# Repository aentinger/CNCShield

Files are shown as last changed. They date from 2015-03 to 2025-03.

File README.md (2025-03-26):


💾 CNC Shield
=============



# 📸 Image

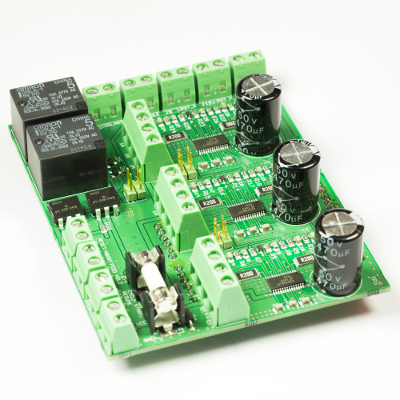
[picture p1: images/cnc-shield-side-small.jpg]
LXRobotics P11 CNC Shield


# 📂 Description

Until very recently the operation of CNC milling machines was reserved mainly for companies and individuals with large budget. However, in the last couple of years, an increasing trend towards self-made (DIY) CNC-milling machines could be observed. As a result from this observation LXRobotics developed the CNC Shield. The CNC-Shield is based on the grbl project, which allows the processing of gcode-control commands and generation of stepper motor control signals for a 3-axis CNC-milling machine with an Arduino Uno.

In order to demonstrate how easy a normal mill can be converted into a CNC mill we decided to convert the Proxxon MF70, a very popular milling machine amongst RC enthusiasts, into a full-fledged CNC-milling machine by using our CNC shield. The conversion with all necessary steps is well documented on our blog. Furthermore, extensive tutorials allow easy integration of our CNC  shields in any DIY-CNC project.

**Features**

* Control of 3 bipolar stepper motors with 2.5 A phase current at a maximum of 35 V (e.g.: NEMA17)
* Milling motor and coolant pump can be turned on/off via relays
* Limit switch for X, Y and Z-axis can be attached
* Cycle Start/Resume, Feed Hold and Reset/Abort switches can be attached
* grbl-compatible
* High qualits screw terminals for stable and durable connection of cables to the board
* 8A Fuse on board

Note
* Active cooling of the stepper motor driver is recommended.

# 🎥 [Video](images/cnc_shield_demo.mp4)

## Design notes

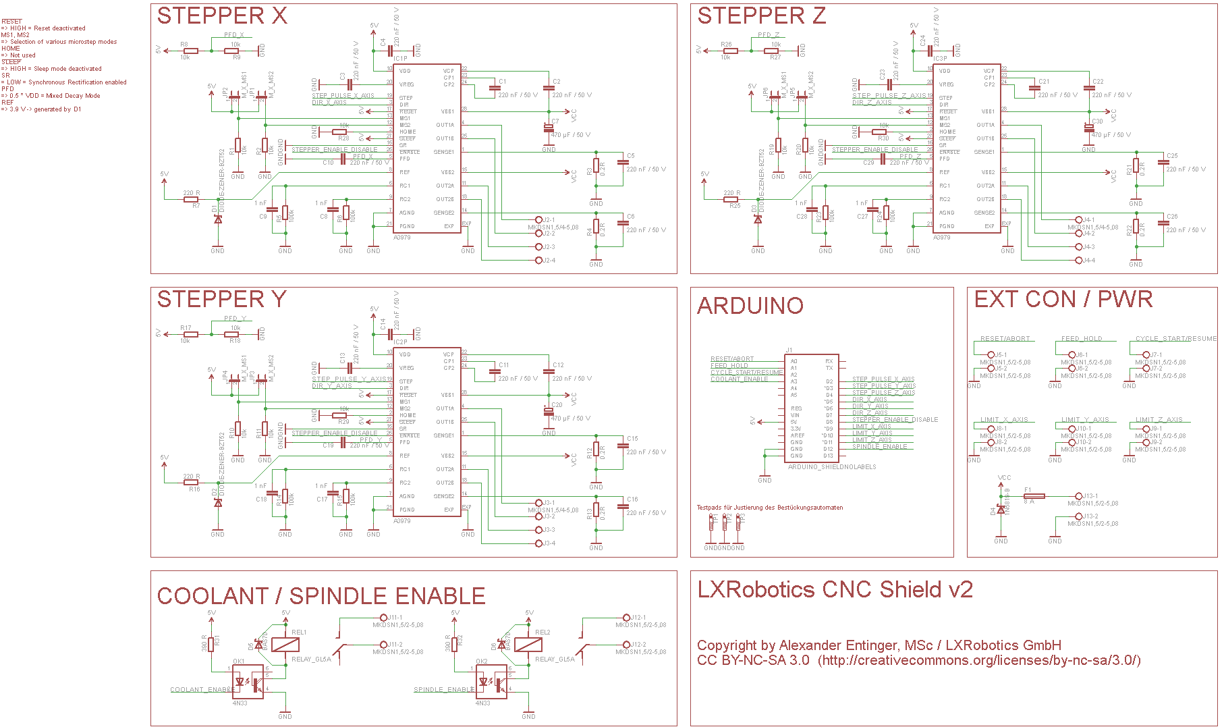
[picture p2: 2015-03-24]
hardware/lxrobotics_cnc_shield_v2.png

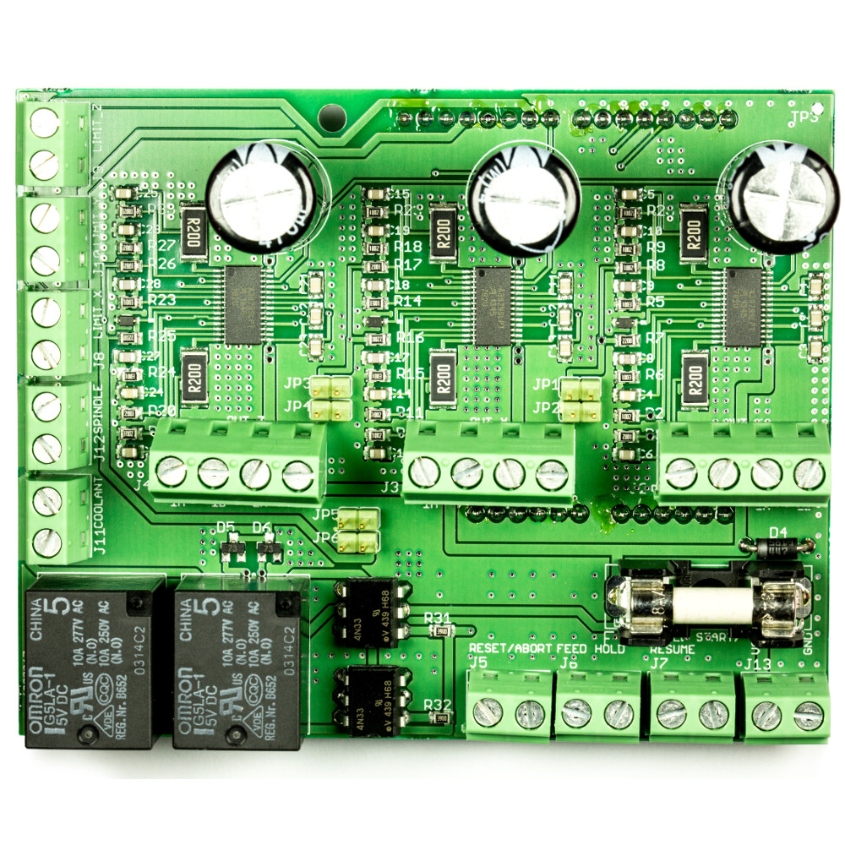
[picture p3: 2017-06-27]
images/cnc-shield-top-large.jpg

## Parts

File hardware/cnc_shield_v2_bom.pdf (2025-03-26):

Menge | Schaltplan | Bezeichnung | Farnell Bestell Nummer | Preis (1 Stück) | Gesamtpreis | Wird bestückt | Footprint | Säckchen
3 | IC1P,IC2P,IC3P | A3979, Stepper-Motortreiber, 2.5 A, 35 V, TSSOP28 | 1521716 | € 9,31 | € 27,93 | x
3 | | Kühlkörper für A3979 | 4302175 | € 0,81 | € 2,43 | | | S1
2 | J1 | Arduino Stiftleisten, 1x6, 2.54 mm | 1022255 | € 0,37 | € 0,74 | | | S2
2 | J1 | Arduino Stiftleisten, 1x8, 2.54 mm | 1022257 | € 0,19 | € 0,38 | | | S2
21 | C1,C2,C3,C4,C5,C6,C10,C11,C12,C13,C14,C15,C16,C19,C21,C22,C23,C24,C25,C26,C29 | Kondensator, 220 nF, 50V, 0805 | 2320842 | € 0,05 | € 0,97 | x
15 | R1,R2,R8,R9,R10,R11,R17,R18,R19,R20,R26,R27,R28,R29,R30 | Widerstand 10 k, 0805 | 1469856 | € 0,02 | € 0,33 | x
6 | JP1,JP2,JP3,JP4,JP5,JP6 | Stiftleiste, 2 Polig, 2.54 mm | 3418285 | € 0,24 | € 1,44 | | | S2
6 | | Jumper, 2 Polig, 2.54 mm | 4218176 | € 0,14 | € 0,84 | | | S2
6 | R3,R4,R12,R13,R21,R22 | Widerstand 0.2R, 2W, 2512 | 2328177 | € 0,26 | € 1,55 | x
3 | J2,J3,J4 | Schraubklemme, 4 Polig, MKDS 1,5/4-5,08 | 3041542 | € 1,94 | € 5,82 | | | S3
3 | C7,C20,C30 | Aluminium-Elko, 470 uF, 50 V | 1902936 | € 0,35 | € 1,06 | | | S4
6 | R5,R6,R14,R15,R23,R24 | Widerstand, 0805, 100 kOhm | 9332405 | € 0,01 | € 0,04 | x
6 | C8,C9,C17,C18,C27,C28 | Kondensator, 1 nF, 100 V, 0805 | 1759287 | € 0,02 | € 0,11 | x
3 | D1,D2,D3 | Z-Diode, BZT52, 3.9V, 5 mA | 2077925 | € 0,05 | € 0,15 | x
3 | R7,R16,R25 | Widerstand, 0805, 220 R | 9334130 | € 0,01 | € 0,02 | x
9 | J5,J6,J7,J8,J9,J10,J11,J12,J13 | Schraubklemme, 2 Polig, MKDS 1,5/2-5,08 | 3041440 | € 0,81 | € 7,31 | | | S3
1 | D4 | 1N5819, Vreverse = 40 V, If = 1 A | 9801219 | € 0,22 | € 0,22 | | | S5
2 | D5,D6 | BAS70, Diode Shottkey, Relais Freilaufdiode | 1797834 | € 0,09 | € 0,17 | x
2 | R31,R32 | Widerstand, 0805, 390 Ohm | 9334475 | € 0,01 | € 0,01 | x
2 | REL1,REL2 | GL5A Leistungsrelais, 5 VDC, 250 V AC, 10 A, RCOIL = 70 R | 1455502 | € 1,43 | € 2,86 | | | S6
2 | OK1,OK2 | 4N33, Optokoppler mit Photo-Darlington, DIL06 | 1469601 | € 0,45 | € 0,90 | | | S5
1 | F1 | Sicherungshalter 5 x 20 mm | 1162740 | € | 0,56 | € | 0,56 | S2
1 | F1 | Sicherung, 5x20, 8A, 250 V | 1354596 | € | 0,65 | € | 0,65
1 | Leitfähiger Schaumstoff | 1687855 | € | 2,40 | € | 2,40 | - | Bestellung von 1 Stück für 50 CNC Shields ausreichend
Summe | € | 58,90

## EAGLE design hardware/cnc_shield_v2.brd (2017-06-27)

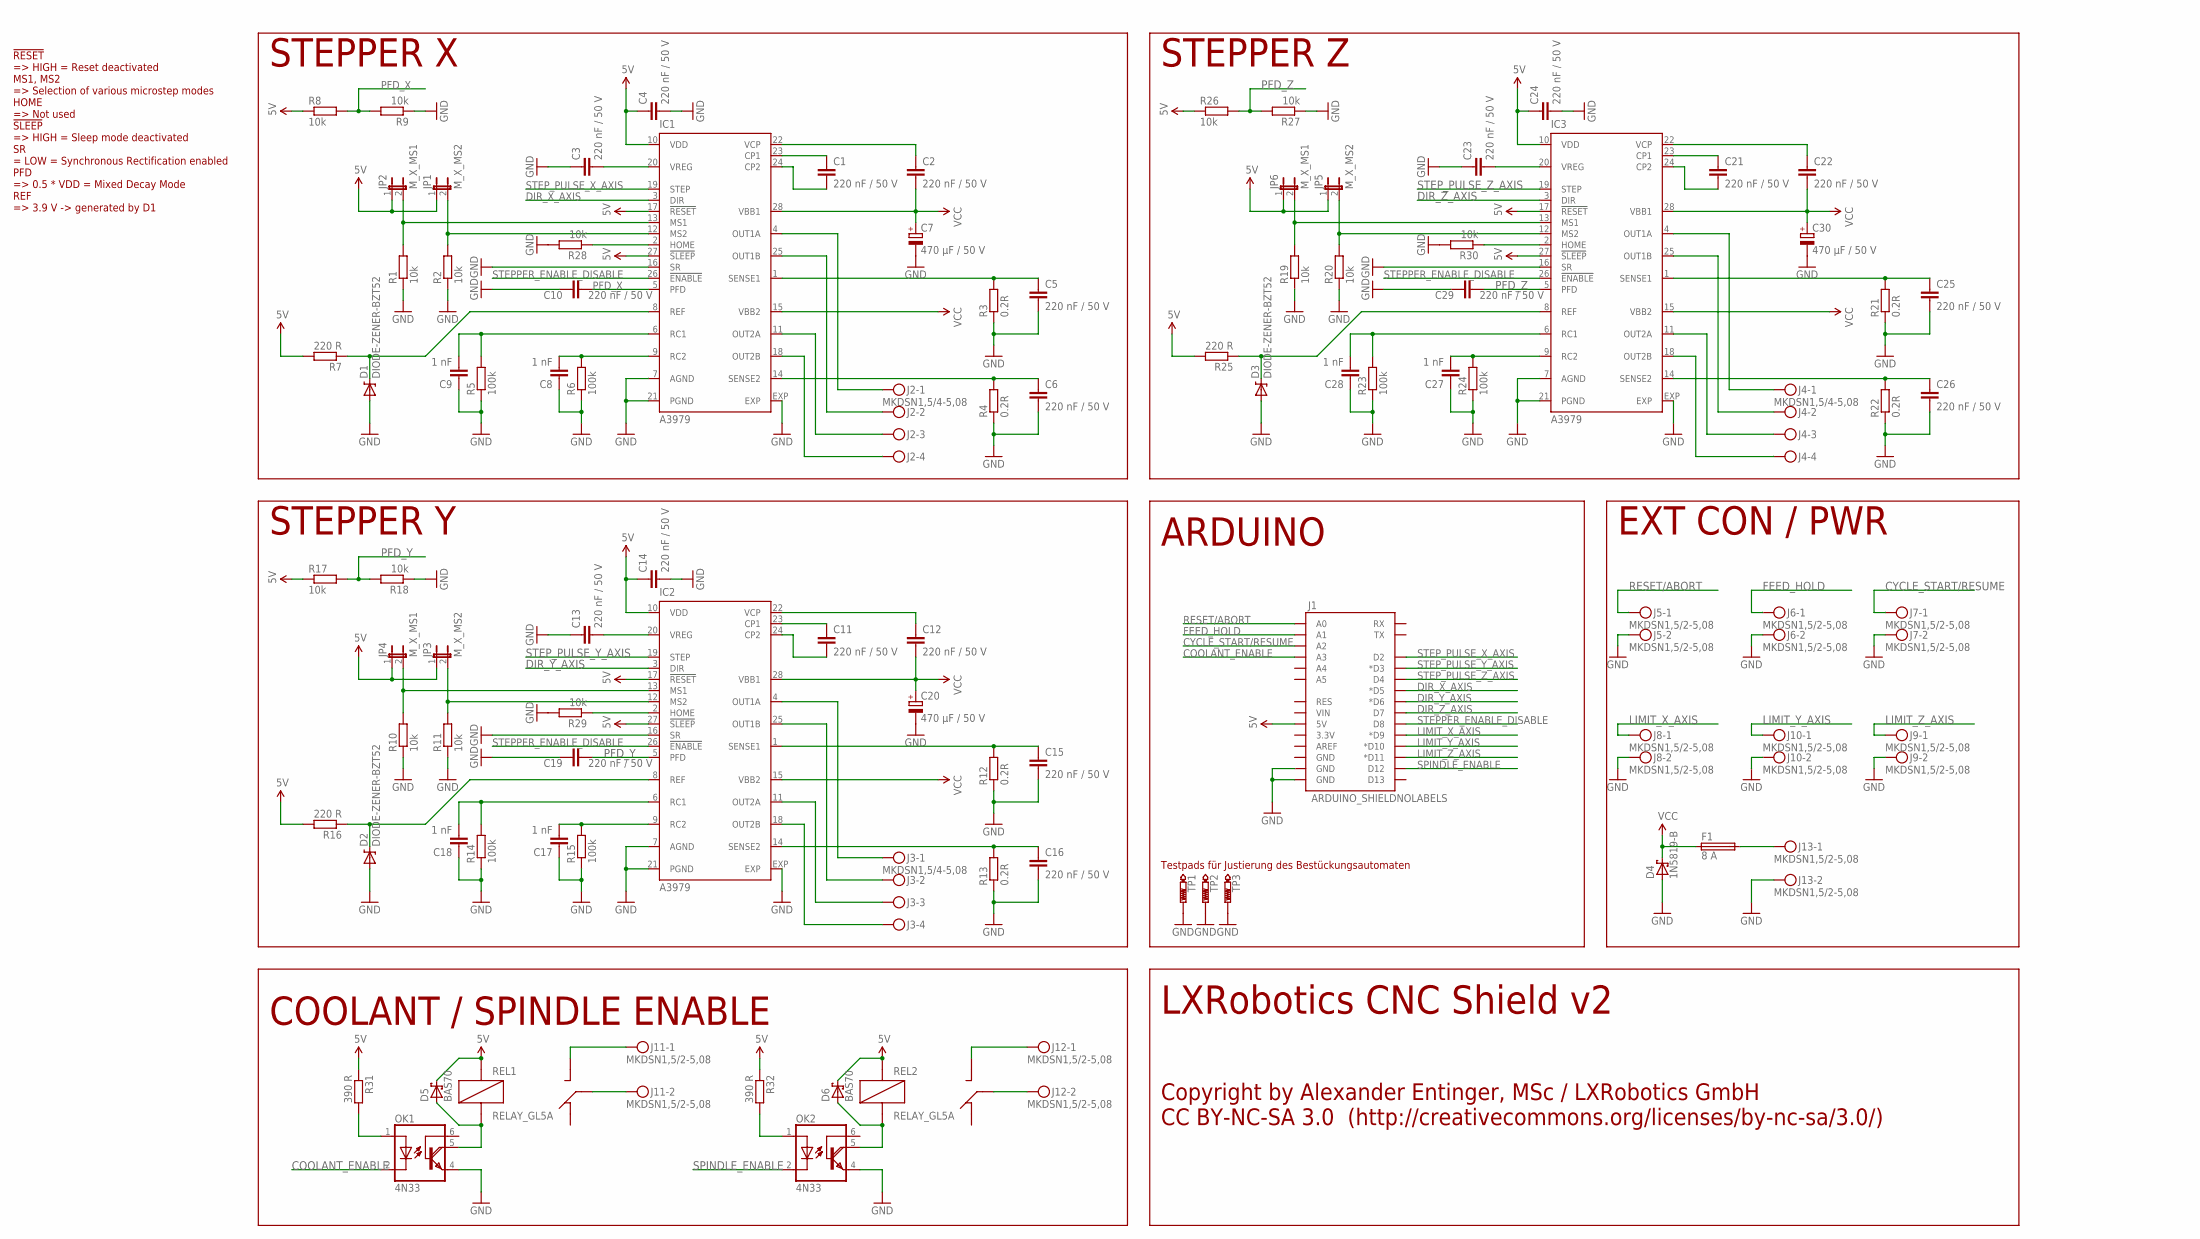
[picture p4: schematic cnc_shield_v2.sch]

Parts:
C1, C2, C3, C4, C5, C6, C10, C11, C12, C13, C14, C15, C16, C19, C21, C22, C23, C24, C25, C26, C29: 220 nF / 50 V; C0805K
C7, C20, C30: 470 µF / 50 V; E5-13
C8, C9, C17, C18, C27, C28: 1 nF; C0805K
D1, D2, D3: DIODE-ZENER-BZT52; SOD-323
D4: 1N5819-B; DO41-7.6
D5, D6: BAS70; SOT23
F1: 8 A; SH22,5
IC1, IC2, IC3: A3979; TSSOP28
J1: ARDUINO_SHIELDNOLABELS; DUEMILANOVE_SHIELD_NOLABELS
J2, J3, J4: MKDSN1,5/4-5,08
J5, J6, J7, J8, J9, J10, J11, J12, J13: MKDSN1,5/2-5,08
JP1, JP3, JP5: M_X_MS2; JP1
JP2, JP4, JP6: M_X_MS1; JP1
OK1, OK2: 4N33; DIL06
R1, R2, R8, R9, R10, R11, R17, R18, R19, R20, R26, R27, R28, R29, R30: 10k; R0805
R3, R4, R12, R13, R21, R22: 0.2R; R2512
R5, R6, R14, R15, R23, R24: 100k; R0805
R7, R16, R25: 220 R; R0805
R31, R32: 390 R; R0805
REL1, REL2: RELAY_GL5A
TP1, TP2, TP3: PTR1B1,27; B1,27

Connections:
5V: C4.1, C14.1, C24.1, D5.3 (C), D6.3 (C), IC1.10 (VDD), IC1.17 (!RESET), IC1.27 (!SLEEP), IC2.10 (VDD), IC2.17 (!RESET), IC2.27 (!SLEEP), IC3.10 (VDD), IC3.17 (!RESET), IC3.27 (!SLEEP), J1.5V, JP1.1, JP2.1, JP3.1, JP4.1, JP5.1, JP6.1, R7.2, R8.1, R16.2, R17.1, R25.2, R26.1, R31.1, R32.1, REL1.R2 (R2_COIL1), REL2.R2 (R2_COIL1)
COOLANT_ENABLE: J1.A3, OK1.2 (C)
CYCLE_START/RESUME: J1.A2, J7.1
DIR_X_AXIS: IC1.3 (DIR), J1.D5 (*D5)
DIR_Y_AXIS: IC2.3 (DIR), J1.D6 (*D6)
DIR_Z_AXIS: IC3.3 (DIR), J1.D7
FEED_HOLD: J1.A1, J6.1
GND: C3.1, C4.2, C5.2, C6.2, C7.-, C8.1, C9.1, C10.1, C13.1, C14.2, C15.2, C16.2, C17.1, C18.1, C19.1, C20.-, C23.1, C24.2, C25.2, C26.2, C27.1, C28.1, C29.1, C30.-, D1.2 (A), D2.2 (A), D3.2 (A), D4.A, IC1.7 (AGND), IC1.16 (SR), IC1.21 (PGND), IC1.EXP, IC2.7 (AGND), IC2.16 (SR), IC2.21 (PGND), IC2.EXP, IC3.7 (AGND), IC3.16 (SR), IC3.21 (PGND), IC3.EXP, J1.GND@0 (GND), J1.GND@1 (GND), J5.2, J6.2, J7.2, J8.2, J9.2, J10.2, J13.2, OK1.4 (E), OK2.4 (E), R1.1, R2.1, R3.1, R4.1, R5.1, R6.1, R9.1, R10.1, R11.1, R12.1, R13.1, R14.1, R15.1, R18.1, R19.1, R20.1, R21.1, R22.1, R23.1, R24.1, R27.1, R28.2, R29.2, R30.2, TP1.TP, TP2.TP, TP3.TP
LIMIT_X_AXIS: J1.D9 (*D9), J8.1
LIMIT_Y_AXIS: J1.D10 (*D10), J10.1
LIMIT_Z_AXIS: J1.D11 (*D11), J9.1
unnamed: C1.1, IC1.23 (CP1)
unnamed: C1.2, IC1.24 (CP2)
unnamed: C2.1, IC1.22 (VCP)
unnamed: IC1.12 (MS2), JP1.2, R2.2
unnamed: IC1.13 (MS1), JP2.2, R1.2
unnamed: C3.2, IC1.20 (VREG)
unnamed: C5.1, IC1.1 (SENSE1), R3.2
unnamed: C6.1, IC1.14 (SENSE2), R4.2
unnamed: IC1.18 (OUT2B), J2.4
unnamed: IC1.11 (OUT2A), J2.3
unnamed: IC1.25 (OUT1B), J2.2
unnamed: IC1.4 (OUT1A), J2.1
unnamed: D1.1 (C), IC1.8 (REF), R7.1
unnamed: C11.1, IC2.23 (CP1)
unnamed: C8.2, IC1.9 (RC2), R6.2
unnamed: C9.2, IC1.6 (RC1), R5.2
unnamed: C11.2, IC2.24 (CP2)
unnamed: C12.1, IC2.22 (VCP)
unnamed: C13.2, IC2.20 (VREG)
unnamed: IC2.12 (MS2), JP3.2, R11.2
unnamed: IC2.13 (MS1), JP4.2, R10.2
unnamed: C15.1, IC2.1 (SENSE1), R12.2
unnamed: C16.1, IC2.14 (SENSE2), R13.2
unnamed: IC2.18 (OUT2B), J3.4
unnamed: IC2.11 (OUT2A), J3.3
unnamed: IC2.25 (OUT1B), J3.2
unnamed: IC2.4 (OUT1A), J3.1
unnamed: C17.2, IC2.9 (RC2), R15.2
unnamed: C18.2, IC2.6 (RC1), R14.2
unnamed: D2.1 (C), IC2.8 (REF), R16.1
unnamed: C21.1, IC3.23 (CP1)
unnamed: C21.2, IC3.24 (CP2)
unnamed: C22.1, IC3.22 (VCP)
unnamed: C23.2, IC3.20 (VREG)
unnamed: IC3.12 (MS2), JP5.2, R20.2
unnamed: IC3.13 (MS1), JP6.2, R19.2
unnamed: C25.1, IC3.1 (SENSE1), R21.2
unnamed: C26.1, IC3.14 (SENSE2), R22.2
unnamed: IC3.18 (OUT2B), J4.4
unnamed: IC3.11 (OUT2A), J4.3
unnamed: IC3.25 (OUT1B), J4.2
unnamed: IC3.4 (OUT1A), J4.1
unnamed: C27.2, IC3.9 (RC2), R24.2
unnamed: C28.2, IC3.6 (RC1), R23.2
unnamed: D3.1 (C), IC3.8 (REF), R25.1
unnamed: IC2.2 (HOME), R29.1
unnamed: IC1.2 (HOME), R28.1
unnamed: IC3.2 (HOME), R30.1
unnamed: D5.1 (A), OK1.5 (COL), REL1.R5 (R5_COIL2)
unnamed: OK1.1 (A), R31.2
unnamed: F1.2, J13.1
unnamed: J11.1, REL1.R3 (R3_SW)
unnamed: J11.2, REL1.R1 (R1_COMMON)
unnamed: D6.1 (A), OK2.5 (COL), REL2.R5 (R5_COIL2)
unnamed: OK2.1 (A), R32.2
unnamed: J12.1, REL2.R3 (R3_SW)
unnamed: J12.2, REL2.R1 (R1_COMMON)
PFD_X: C10.2, IC1.5 (PFD), R8.2, R9.2
PFD_Y: C19.2, IC2.5 (PFD), R17.2, R18.2
PFD_Z: C29.2, IC3.5 (PFD), R26.2, R27.2
RESET/ABORT: J1.A0, J5.1
SPINDLE_ENABLE: J1.D12, OK2.2 (C)
STEPPER_ENABLE_DISABLE: IC1.26 (!ENABLE), IC2.26 (!ENABLE), IC3.26 (!ENABLE), J1.D8
STEP_PULSE_X_AXIS: IC1.19 (STEP), J1.D2
STEP_PULSE_Y_AXIS: IC2.19 (STEP), J1.D3 (*D3)
STEP_PULSE_Z_AXIS: IC3.19 (STEP), J1.D4
VCC: C2.2, C7.+, C12.2, C20.+, C22.2, C30.+, D4.C, F1.1, IC1.15 (VBB2), IC1.28 (VBB1), IC2.15 (VBB2), IC2.28 (VBB1), IC3.15 (VBB2), IC3.28 (VBB1)

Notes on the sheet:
!RESET => HIGH = Reset deactivated MS1, MS2 => Selection of various microstep modes HOME => Not used !SLEEP => HIGH = Sleep mode deactivated SR = LOW = Synchronous Rectification enabled PFD => 0.5 * VDD = Mixed Decay Mode REF => 3.9 V -> generated by D1
STEPPER X
STEPPER Y
STEPPER Z
ARDUINO
EXT CON / PWR
COOLANT / SPINDLE ENABLE
LXRobotics CNC Shield v2
Copyright by Alexander Entinger, MSc / LXRobotics GmbH CC BY-NC-SA 3.0 (http://creativecommons.org/licenses/by-nc-sa/3.0/)
Testpads für Justierung des Bestückungsautomaten

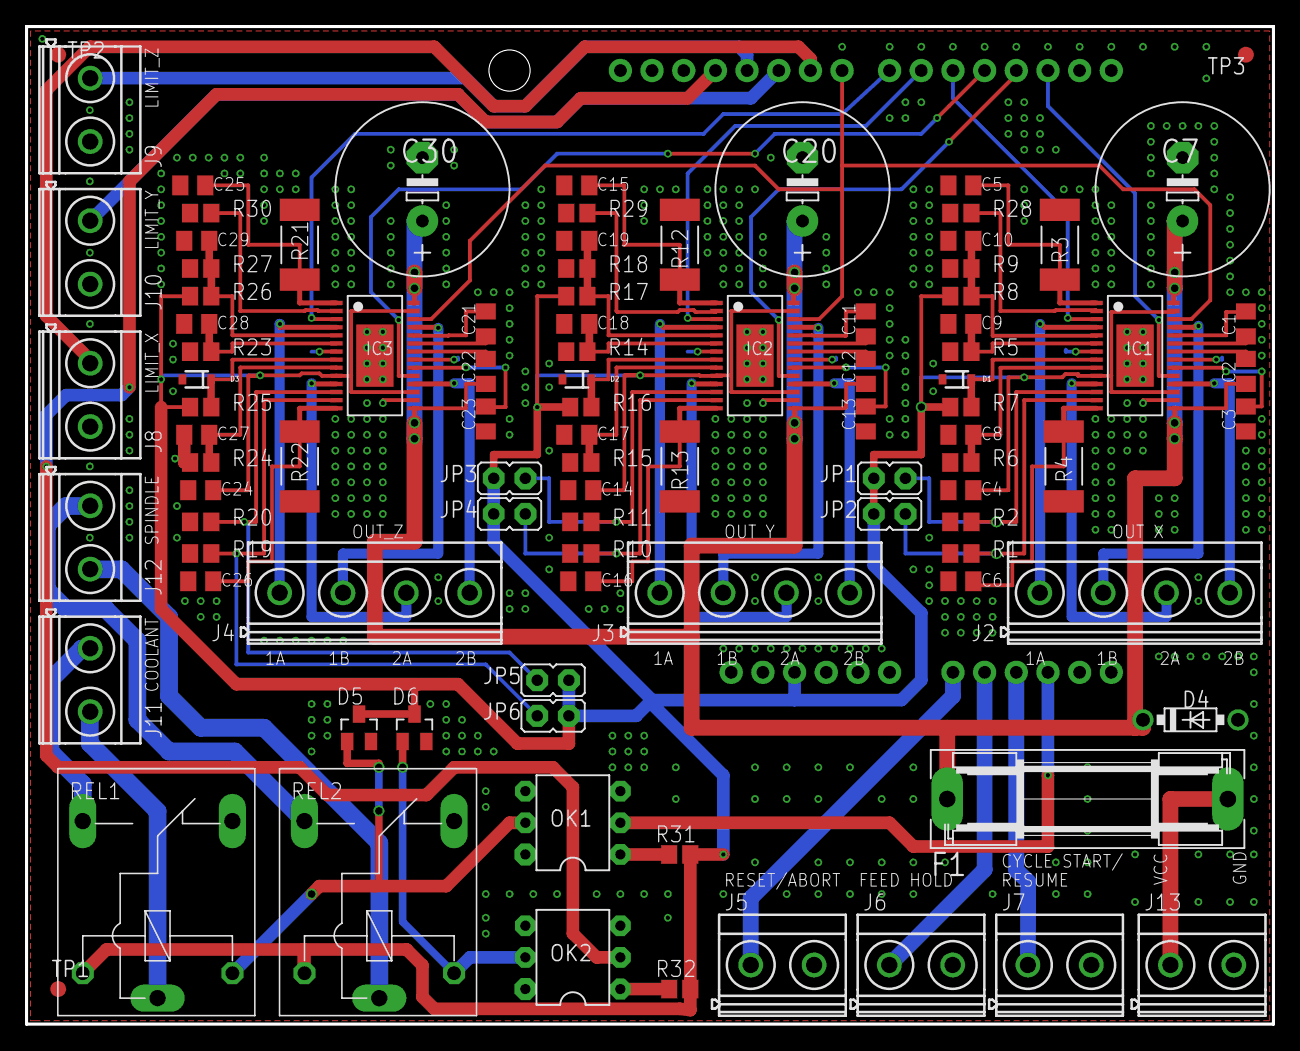
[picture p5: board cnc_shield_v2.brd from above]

Board: 2 copper layers, 100.0 x 80.0 mm, 98 parts (0 on the bottom side), 78 nets.

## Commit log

2014-07-31 deleting grbl.hex (old 0.8 version)
2014-09-17 replacing grbl_v_0_9.hex with latest 0.9 version
2015-03-24 adding v2 version of cnc schield schematic
2017-06-27 Adding hardware + images
    [cnc_shield_v2.brd, cnc_shield_v2.sch]
2025-03-26 Add BOM.

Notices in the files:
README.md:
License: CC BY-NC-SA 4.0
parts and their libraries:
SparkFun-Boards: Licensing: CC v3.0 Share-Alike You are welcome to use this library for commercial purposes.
